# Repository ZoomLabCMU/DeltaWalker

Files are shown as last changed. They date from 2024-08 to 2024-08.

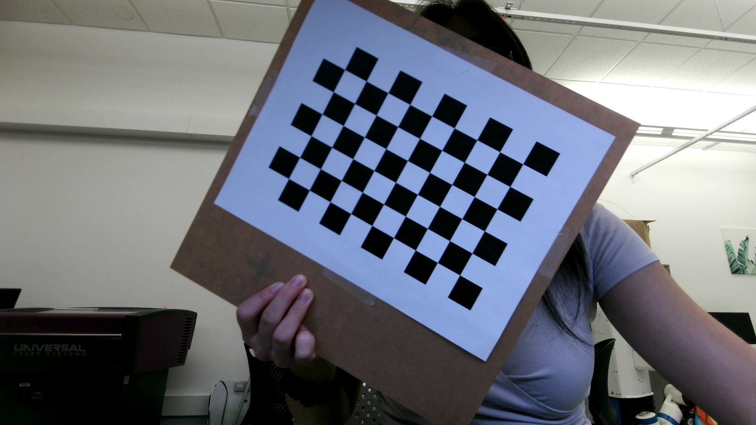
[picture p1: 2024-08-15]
testing/misc/camera_calibration/imgs/calib_30.png

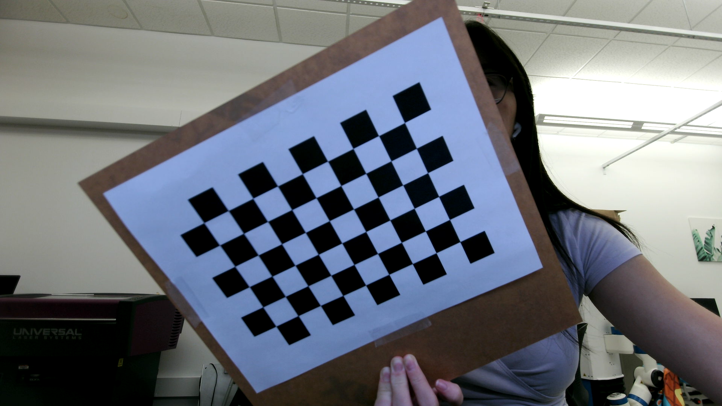
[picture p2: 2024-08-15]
testing/misc/camera_calibration/imgs/calib_4.png

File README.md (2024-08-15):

# DeltaWalker
Jennifer Yang, Zeynep Temel



**About This Project**

For more information about the project, please read Jennifer Yang's Masters Thesis:

https://www.ri.cmu.edu/publications/deltawalker-a-soft-linearly-actuated-delta-quadruped-robot/

This work was funded by the NSF under project Grant No.CMMI-2024794.

**Abstract**

Quadruped robots offer a versatile solution for navigating complex terrain, making them valuable for applications such as industrial automation or search and rescue. Although quadrupeds are more complex than bipeds, they are easier to balance and control and require fewer joints to actuate compared to hexapods. Traditional quadruped designs, however, often feature complex leg mechanisms that are difficult to scale and require many actuators.

We introduce the DeltaWalker, a novel quadruped robot that uses linearly actuated Delta robots as legs. Delta robots offer advantages such as precision and scalability, while still being able to move with three degrees of freedom. This design is inspired by DeltaHands, a 4-fingered hand robot with soft, 3D-printed linear Delta robots. We turn the DeltaHands upside down and adapt the design for locomotion. We explore various gait patterns, including manually designed and trajectory-optimized gaits, evaluated in both simulated and real-world environments. We also describe the system kinematics and investigate other capabilities, such as rotating in place. The findings from these evaluations demonstrate the potential of the DeltaWalker as a simpler, scalable, omnidirectional quadruped robot.

**About This Repo**

This repo contains code for the DeltaWalker Project, both the simulation code and the real-world testing code. 

**BibTeX**
```
@mastersthesis{Yang-2024-142602,
  author = {Jennifer Yang},
  title = {DeltaWalker: A Soft, Linearly Actuated Delta Quadruped Robot},
  year = {2024},
  month = {August},
  school = {Carnegie Mellon University},
  address = {Pittsburgh, PA},
  number = {CMU-RI-TR-24-23},
  keywords = {Delta Robot, Legged Robot, Quadruped Robot, Locomotion, Trajectory Optimization, Gaits},
}
```

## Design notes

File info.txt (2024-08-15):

Assorted files used by multiple folders

helpers - various helper functions
kinematics_delta - single delta kinematics
kineamtics_walker - walker kinematics
ocrl_paths - trajectory conversion class for trajectory optimized trajectories
path_gen - path generation class for manually designed trajectories
trajectories - manually designed trajectories

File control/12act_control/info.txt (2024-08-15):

12 actuator control code for computer to walker via cable
keyboard_operation - teleoperation
manual_traj_operation - commanding manually designed trajectories
ocrl_traj_operation - commanding trajectory-optimized trajectories
control_helpers - assorted helper functions for commanding trajectories
DeltaWalker - serial communication between computer and robot

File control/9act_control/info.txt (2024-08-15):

9 actuator control code for computer to walker via wifi
based on https://github.com/iamlab-cmu/DeltaHands

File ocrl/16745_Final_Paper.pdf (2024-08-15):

# Trajectory Generation for a Linearly Actuated Delta Quadruped Robot

Jennifer Yang
Robotics Institute
Carnegie Mellon University Pittsburgh, PA
jennifey@andrew.cmu.edu

Alfred Chang
Department of Mechanical Engineering Carnegie Mellon University Pittsburgh, PA
alfredc@andrew.cmu.edu

Jon Yeo
Department of Mechanical Engineering Carnegie Mellon University Pittsburgh, PA
jongwony@andrew.cmu.edu

Abstract—This paper introduces Delta Walker, a soft quadruped robot employing four 3D-printed prismatic delta robots. Initially designed as a hand-like manipulator, the Delta Walker operates within a diamond-shaped arrangement about its origin and exhibits compliant behavior due to the presence of soft links. The primary focus of this work lies in utilizing nonlinear trajectory optimization to generate walking trajectories for Delta Walker, which are subsequently verified through simulation using the inverse kinematics of the delta robots. The outcomes of this research contribute to advancements in control strategies for walking quadruped robots, particularly in trajectory optimization and simulation verification using inverse kinematics. Index Terms—prismatic delta robot, DIRCOL, trajectory optimization

I. INTRODUCTION

Delta Walker, Fig. 1, is a quadruped robot that uses 4 soft, 3D printed prismatic delta robots arranged in a diamond shape about the origin of the robot. It is approximately 15 cm × 15 cm wide and ranges from approximately 15 cm to 17 cm tall, depending on the motor actuation amounts. The robot initially operates as a hand-like manipulator, where the delta robots are configured as fingers to simulate dexterous hands with parallel fingertips. The parallelism and translational motions of these delta robots facilitate fingertip control, and the presence of soft links adds a degree of compliance [1]. In this paper, we present a method for trajectory optimization for the Delta Walker. We generate multiple trajectories that can be repeated for many iterations on robot to create full walking gaits. We ran these trajectories in simulation to verify that they would not cause the robot to fall over.

II. RELATED WORKS

The field of walking quadruped robots has seen significant advancements in control strategies aimed at achieving agile and robust locomotion. Various approaches have been explored to address the complexities of controlling multi-legged systems in diverse environments.
One notable focus in recent research has been on reinforcement learning (RL) algorithms for controlling quadruped robots. RL offers the advantage of learning controllers without explicit modeling of system dynamics, making it suitable

This work was funded by the NSF under project Grant No.CMMI-2024794.

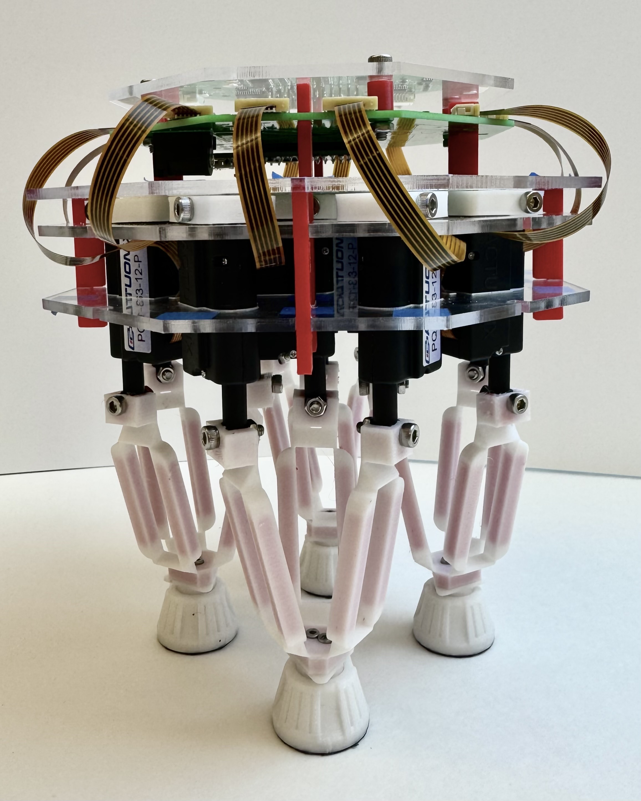
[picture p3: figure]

Fig. 1: Delta Walker

for handling noisy observations and controls. Platforms like RealAnt have been developed specifically for real-world reinforcement learning research, enabling the validation and evaluation of state-of-the-art RL algorithms on physical platforms [2].
Optimization-based control strategies have also played a crucial role in achieving robust locomotion for quadruped robots. These strategies include predictive controllers that reason about consequences iteratively and reactive controllers that focus on immediate actions. Model-based approaches offer advantages in safety considerations and generalization but face challenges in integrating perceptual streams [3]. Efforts have also been made to enhance the mechanical and electrical components of quadruped robots. Designs such as HAMR-F leverage advances in manufacturing, sensing, and energy storage to improve mechanical robustness, variable gait control, and payload capacity. These advancements contribute to achieving faster locomotion, improved heading control, and dynamic gaits with aerial phases [4].
Additionally, the development of low-cost and scalable quadruped robot platforms has opened avenues for research and education in control algorithms. Platforms like MIT minicheetah, Solo, and Stanford Doggo offer affordable options for exploring motion planning controllers and reinforcement learning in real-world settings [5]–[7].
The integration of advanced control algorithms with innovative hardware designs has paved the way for tackling challenges such as terrain adaptability, speed limitations, and payload capacity in walking quadruped robots. Ongoing research continues to focus on improving sample efficiency, safe exploration, and real-time adaptation of control strategies for agile and versatile locomotion in various environments. Overall, the interdisciplinary efforts in controls for walking quadruped robots encompass a wide range of techniques, from reinforcement learning and optimization-based strategies to mechanical enhancements and low-cost platform development, driving advancements in robotic locomotion and autonomy.

III. TRAJECTORY OPTIMIZATION

A. IPOPT

We chose the Interior Point OPTimizer solver – also termed IPOPT – as our solver of choice. This solver is meant for large scale non-linear optimization problems of continuous systems. We chose this solver because it fit with our problem setup of a quadratic cost function with a quadratic constraint. It is worth noting that all but the body torque constraint were linear constraints. The body torque constraint as specified in the Constraints section later is a function of both relative feet positions and the ground contact forces. Future work could target methods for reframing this constraint as a linear constraint to speed up computation.

B. Dynamics

Our system is represented by five point masses: one for the body and one for each foot. The state comprises the positions and velocities in the x, y, and z axes of these masses, resulting in a total of 12 degrees of freedom and 30 states. The system is governed by four control inputs, corresponding to forces along each leg. The ordering of the state and control vectors is as follows:

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
where p

(i)
is the position of the body or foot i in each axis, v

(i)
is the velocity of the body or foot i in each axis, and F

(i)
is the force along leg i.

We formulated our system dynamics as a linear equation governing forces:

mbI
mf I
mf I
mf I
mf I

v˙b
vf˙1
vf˙2
vf˙3
vf˙4

=

−m¨bg
−m¨f1
g
−m¨f2
g
−m¨f3
g
−m¨f4
g

+

−I −I −I −I
I | 0 | 0 | 0
0 | I | 0 | 0
0 | 0 | I | 0
0 | 0 | 0 | I

F1
F2
F3
F4

+

0 0 0 0
I 0 0 0
0 I 0 0
0 0 I 0
0 0 0 I

λ1
λ2
λ3
λ4

(2)

where mb is the mass of the body, mf is the mass of each foot, and λi

is the contact force on foot i.

C. Cost Function
We experimented with two different cost functions to evaluate their performance and found that Eqn. 4 yielded significantly better results.

J(x1:N , u1:N−1) =

N

X⁻¹

i=1

1
2

||xi − xg||²
2 +

1
2

||ui

||²
2
+

1
2

||xN − xg||²
2

(3)

The first cost function comprises a cost term for the distance between the current state and the goal state, along with a cost term for the internal body-to-foot forces. The state error cost term encourages the solver to reach the goal state quickly, as earlier attainment results in reduced net state error. The internal force cost term promotes lower overall control costs to minimize control effort and the forces sustained by the actuators. However, this cost function required the solver to take 2.5 times longer to generate a trajectory with minimal error compared to the subsequent cost function.

J(x1:N ) = X

N

i=1

1
2

||xi − xg||²
2

(4)

This cost function penalizes solely the error between the current state and the goal state, driving the solver to find a swift solution to reach the goal state without considering penalties for the control forces within the body. Utilizing this cost function, the solver produced the same trajectory, within minor tolerance, 2.5 times faster than Eqn. 3. Consequently, we employed this cost function for our optimization problem.

D. Optimization Problem & Constraints
In our problem setup, we employ a predefined set of knot points where one foot is permitted to be lifted off the ground while the other feet remain fixed to the ground. These knot points are stored in vectors named M0, M1, M2, M3, and M4, where the number designates which foot is permitted to be lifted off the ground, with M0 indicating that all four feet must maintain contact with the ground. The inclusion of M0 allows the robot sufficient time to shift its weight into the support polygon in preparation for the subsequent step.
The constraints applied to the optimization problem are as follows:

min

x1:N

J(x1:N )

1) Initial and goal state constraint:
| st x1 = xic | (1)
| xN = xg | (2)

Initial and goal constraints are used to dictate the starting and end states that the solver will optimize the trajectory for.
2) Dynamics constraint:

xk+1 = dynamics(xk, uk, λk) for k ∈ [1, N − 1] (3)

To guarantee adherence to the modeled dynamics during simulation, we impose an equality constraint on each subsequent state, derived from the dynamics solution of the preceding state.
3) Body height constraint:

0.053 ≤p

(b)
z ≤ 0.0605 for body z-height, k ∈ [1, N] (4)

To prevent the body from falling to the ground or flying into the sky, we apply a primal constraint on the z-height of the body position. The maximum z-height prevents scenarios where the robot flies into the sky and all feet lift off the ground. Conversely, the minimum z-height prevents the body from sinking too close to the ground, hindering the legs’ ability to lift. We set the maximum range of motion from 4.8cm to 6.8cm in height, and constrain the z-height of the robot body between 5.3cm and 6.05cm. This buffer ensures that the robot remains in a state where the legs can be lifted off the ground.
4) Foot height constraint:

p

(i)
z | ≥ 0 for i=1,2,3,4, k ∈ [1, N] | (5)

To prevent the foot from falling into the ground, we place a primal constraint on the z-height of the foot position.
5) Foot speed inequality constraint:

||v

(i)
||2 ≤ 0.015 for i=1,2,3,4, k ∈ [1, N] | (6)

Based on the physical specifications of the delta’s linear actuators, we impose a maximum speed of 15 mm/s on each foot.
6) Grounded foot velocity constraint:

||v

(i)
||2 = 0 for grounded foot, k ∈ [1, N] (7)

To prevent the solver from modeling frictionless contact, we apply a primal bound zero-velocity constraint on the feet that are determined to be fixed to the ground. It is reasonable to implement a zero-velocity constraint because the contact forces realizable by the motors are small compared to the body mass. This assumption also simplifies computation by eliminating the need to model a friction cone constraint.

7) Grounded foot z-height constraint:

p

(i)
z | ≤ 0.00025 for the grounded feet, k ∈ [1, N] | (8)

To further ensure that the robot never enters a dynamically unstable mode by lifting more than one foot, we enforce primal bound z-height constraint on the three feet that are meant to be grounded as dictated by the M’s. Without this constraint, we noticed that the solver would create a trajectory where multiple feet are lifted.
8) Ground contact force constraint:

λ

(i)
z | ≥ 0 for i=1,2,3,4, k ∈ [1, N − 1] | (9)

Since ground forces can only apply a normal force to an object in contact and cannot apply any force when an object is not in contact, we apply a constraint where the ground forces are non-negative if a foot is in contact with the ground, and a constraint where the ground force is zero if a foot is in the air.
9) Floating foot contact force constraint:

λ

(i)
z | = 0 for lifted feet k ∈ [1, N − 1] | (10)

Since the ground cannot exert a normal force on a foot that it is not in contact with, we place a primal bound on the lifted feet to ensure that the force is zero.
10) Body torque equality constraint:
X

4

i=1

λ

(i) × (p
(i) − p

(b)
) = 0 for k ∈ [1, N − 1] (11)

To prevent the body from reaching a state where it could tip over, we apply a net-zero torque constraint around the body center of mass (COM). This ensures that the body remains within the support polygon and never tips over. It’s worth noting that this constraint is the only quadratic constraint in our optimization problem. All other constraints in our optimization problem are linear constraints.
11) Foot position inequality constraints:

∥p

(ai)
x,y − p

(i)
x,y∥2 ≤ 0.0135 | (12)

p

(i)
z ≥ −0.0025 + (p

(ai)
z | − 0.058) | (13)

p

(i)
z ≤ 0.0075 + (p

(ai)
z | − 0.058) | (14)

for foot i, for k ∈ [1, N]

The Foot Position Inequality Constraints take the shape of a cylinder, with the circle in the x, y-plane, that moves in
the global frame fixed relative to p | (ai)
for each foot i. The
(p

(ai)
z − 0.058) serves as a z-offset for the lower and upper z bounds of the cylinder to translate with, as p
| (ai) | is initially
0.058 meters above the ground. The cylindrical bounds are determined based on the workspace of the delta actuator’s end effector, visualized as the space between two upward-facing convex paraboloids.
This cylindrical constraint restricts vertical motion of the body along the z axis in tandem with the other constraints.

As the cylinder moves in tandem with p

(ai)
(and consequently
with p

b
), exceeding a 0.0025-meter lift would elevate the cylinder above ground level, potentially conflicting with the Grounded Foot Z-Height Constraint. Conversely, lowering the body by more than 0.0075 meters would submerge the cylinder entirely below ground, rendering no feasible p

(i)
according to
the Foot Height Constraint.

IV. SIMULATION
The trajectory positions generated by the solver are in the world frame, where the ground plane is set to be z = 0. However, to calculate the motor actuation amounts to control the Delta Walker, these positions were shifted to the robot frame. For this, the z = 0 plane was shifted up to be coincident with the base plane of the robot, and the feet were placed on the negative z-axis. This adjustment was made to simplify the kinematic calculations. The motor actuation amounts for each delta were calculated using inverse kinematics for delta robots, considering the desired position of the COM and feet at each timestep. These actuation amounts were then input into the simulation environment.

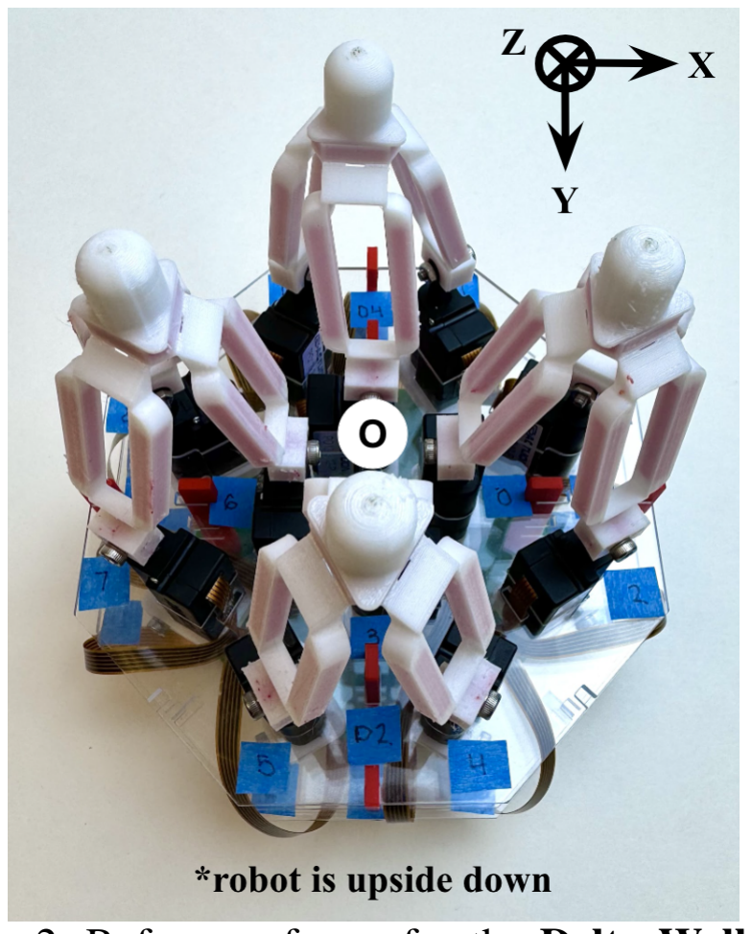
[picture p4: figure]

Fig. 2: Reference frame for the Delta Walker

The simulation of the Delta Walker was developed in Pybullet [8] using a simplified URDF model of the robot, as shown in Fig. 3, and set in the world frame. The objective of the simulation was to verify that the generated trajectories were quasi-statically stable and that the robot could reach the goal point. To simulate the motor actuation commands, we utilized Pybullet’s built-in P controller. We inputted the desired motor actuation amounts and imposed limits on the maximum force and velocity of the actuators to ensure realistic movement. Although the real robot employs a PID controller to command the motors, the built-in P controller sufficed for simulation purposes. Given that the trajectories should be quasi-statically stable and the robot moves slowly in the real world, we did not prioritize optimizing the simulated robot speed. We were able to track the world frame positions of the

COM and the feet of the robot in simulation and compared them to the desired positions of the robot from the generated trajectory.

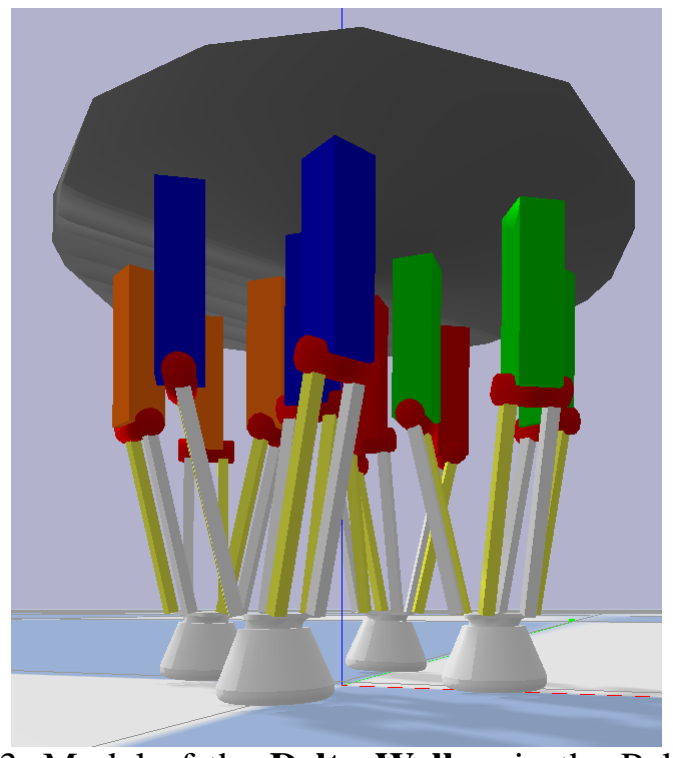
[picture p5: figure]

Fig. 3: Model of the Delta Walker in the Pybullet

V. RESULTS AND DISCUSSION
We generated three different trajectories with varying goal states and knot points. In the simulation, we tracked the positions of each point mass and calculated the mean square error of their positions. These variations and their resulting errors are listed in Table I. The feet were stepped in the order of Foot 3, Foot 2, Foot 4, and Foot 1.

TABLE I: Trajectory Generation Results

Trajectory Info | Mean Square Error (mm)
Label | Goal | Knot Points | Eb | E1 | E2 | E3 | E4
A | (20, 20, 53) | 40 | 8.0 | 7.7 | 7.7 | 7.0 | 7.0
B | (10, 10, 53) | 40 | 1.8 | 1.6 | 1.9 | 1.8 | 1.6
C | (20, 20, 53) | 80 | 3.0 | 3.8 | 4.6 | 3.0 | 3.1

Goal the goal position (x, y, z) of the body COM in mm.

For trajectories A and B, we opted to use 40 knot points, corresponding to each foot taking one step. For trajectory C, we chose to use 80 knot points, corresponding to each foot taking two steps. In trajectories A and C, we set the desired COM position to be 0.02 m away from the origin in the x and y axes. In trajectory B, we set the desired COM position to be closer to the origin, at 0.01 m away in the x and y axes. Trajectories B and C would take steps of size 0.01 m to reach the final point, whereas trajectory A would take a step of size 0.02 m.
Trajectory A, as shown in Fig. 4, exhibits the largest error. This occurred because the desired end point was too distant from the starting point, causing the actuators to reach their limits and the robot to take the maximum possible step. Additionally, the support polygon decreased in size after the first two steps, leading to tilting by the time the third foot (Foot 4) stepped in the sequence. Although it was meant to be

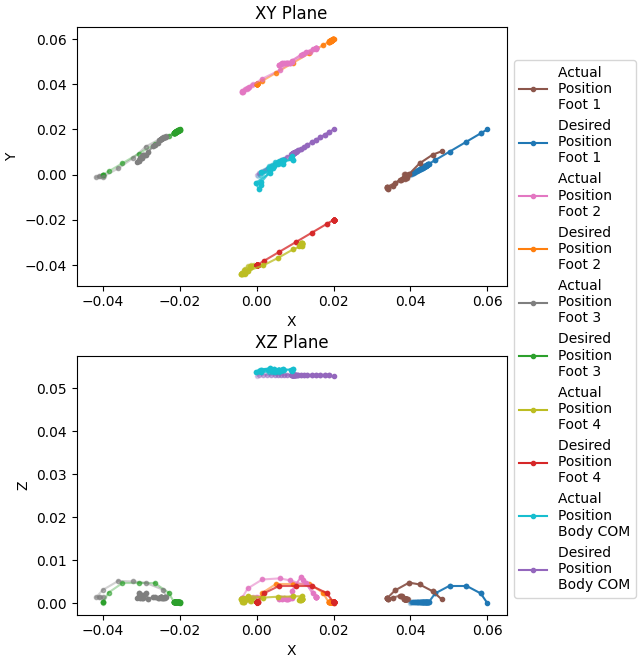
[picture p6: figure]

Fig. 4: Trajectory A Results

in the air, the robot leaned on that foot, resulting in instability and pushing rather than a stable step.

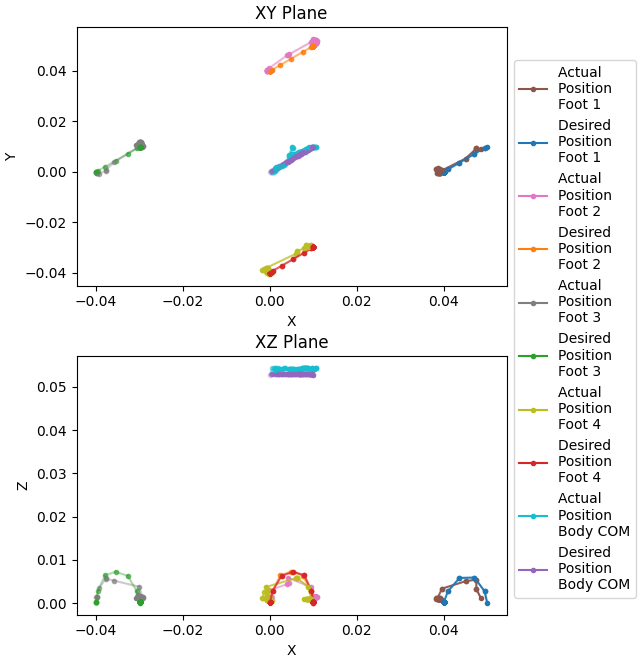
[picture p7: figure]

Fig. 5: Trajectory B Results

The error significantly improved with a smaller step size. Trajectory B, as depicted in Fig. 5, exhibits the smallest error among all trajectories. This improvement is attributed to the fact that the desired end point was within reach within the trajectory, ensuring that the actuator limits were not exceeded. Additionally, the support polygon remained wider, reducing the risk of the robot tipping over. Each foot lifted as expected, resulting in a stable step.

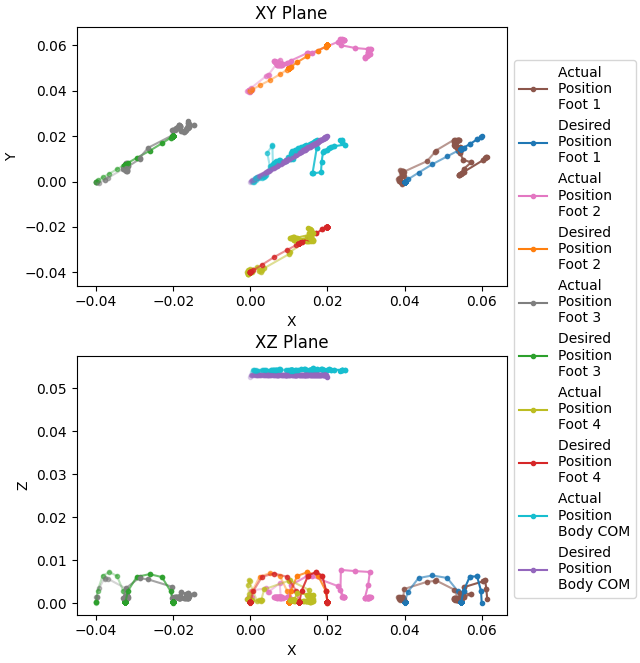
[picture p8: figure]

Fig. 6: Trajectory C Results

The error worsened when taking two steps despite the smaller step size. Trajectory C, illustrated in Fig. 6, exhibited better performance than Trajectory A but worse than Trajectory B. During the first set of steps, the second foot to lift (Foot
2) did not actually lift as the robot tilted towards it. Likewise, during the second set of steps, the third foot to lift (Foot 4) encountered the same issue. The steps were less stable because the generated trajectory had varying step sizes for each foot.

VI. CONCLUSIONS

We utilized trajectory optimization to generate three different trajectories for walking for the Delta Walker. We varied the goal states and knot points, allowing experimentation with the number of steps and step sizes. We found that using a smaller step size and generating only one set of steps was better for creating a quasi-statically stable gait. By repeating this gait multiple times, the robot has the potential to move far. Although taking larger steps or more sets of steps was not quasi-statically stable, they were still trajectories stable enough that the robot did not fall over, and the robot did progress forward towards the goal state. The gaits we generated and the parameters we experimented with will inform how to approach generating more gaits in the future.

VII. FUTURE WORK

One significant area of improvement is reducing solve time. Currently, the solver takes around 25 minutes to generate a trajectory with 40 knot points and 75 minutes to generate a trajectory with 80 knot points. Speed improvements can be found in a couple of areas. First, it may be possible to reformulate the Body Torque constraint, which is present to prevent the body from tipping over, into a linear constraint form. This would help simplify the complexity of the problem and allow us to use a linear optimization solver. Second, there may be other nonlinear optimizers that perform better for our problem size. The main reason we chose IPOPT over other solvers was that we were most familiar with it.
Additional work can be done to make the robot walk faster. We can explore relaxations on the body height constraint and foot position constraints to allow the robot to actuate closer to its limits. Additionally, for a more accurate model, we could model the contact patches more accurately using the geometric shape of the robot feet as opposed to just the current point mass model. Furthermore, we can explore different foot orderings to find a better walking gait or discover other types of gaits.
Beyond simulation, we can also apply this to the real robot and run tests to quantify the movement of the robot. We can run multiple iterations of the same trajectory and observe how far the robot moves not just in one set of steps but in multiple sets of steps, or combine different trajectories to create more complicated paths.

CODE AND VIDEOS

This research has not been published yet, so we cannot share the code at this time. However, videos of the trajectories in simulation, as well as some preliminary testing that has been done on the real robot, can be found here: https://tinyurl.com/ocrl-delta-walker. (https://drive.google.com/drive/folders/1QLCxWCHY97KjzdRRpfBpueAbO3D2707O?usp=sharing)

ACKNOWLEDGMENT

This research is associated with CMU’s Zoom Lab, led by Professor Zeynep Temel. The authors sincerely thank Professor Zeynep Temel, Professor Zachary Manchester, Arun Bishop, Zilin Si, and Sarvesh Patil for their assistance with this project.

REFERENCES

[1] Z. Si, K. Zhang, O. Kroemer and F. Z. Temel, ”DeltaHands: A Synergistic Dexterous Hand Framework Based on Delta Robots,” in IEEE Robotics and Automation Letters, vol. 9, no. 2, pp. 1795-1802, Feb. 2024, doi: 10.1109/LRA.2024.3349920.
[2] R. Boney, et al., ”RealAnt: An Open-Source Low-Cost Quadruped for Education and Research in Real-World Reinforcement Learning,” 2022. [Online]. Available: https://arxiv.org/abs/2011.03085.
[3] P. M. Wensing, M. Posa, Y. Hu, A. Escande, N. Mansard and A.
D. Prete, ”Optimization-Based Control for Dynamic Legged Robots,” in IEEE Transactions on Robotics, vol. 40, pp. 43-63, 2024, doi: 10.1109/TRO.2023.3324580.
[4] B. Goldberg et al., ”Power and Control Autonomy for High-Speed Locomotion With an Insect-Scale Legged Robot,” in IEEE Robotics and Automation Letters, vol. 3, no. 2, pp. 987-993, April 2018, doi: 10.1109/LRA.2018.2793355.
[5] B. Katz, J. D. Carlo and S. Kim, ”Mini Cheetah: A Platform for Pushing the Limits of Dynamic Quadruped Control,” 2019 International Conference on Robotics and Automation (ICRA), Montreal, QC, Canada, 2019, pp. 6295-6301, doi: 10.1109/ICRA.2019.8793865.
[6] Kim, D., Carlo, J.D., Katz, B., Bledt, G., & Kim, S. (2019). Highly Dynamic Quadruped Locomotion via Whole-Body Impulse Control and Model Predictive Control. ArXiv, abs/1909.06586.
[7] C. Gehring, S. Coros, M. Hutter, M. Bloesch, M. A. Hoepflinger and
R. Siegwart, ”Control of dynamic gaits for a quadrupedal robot,” 2013 IEEE International Conference on Robotics and Automation, Karlsruhe, Germany, 2013, pp. 3287-3292, doi: 10.1109/ICRA.2013.6631035.
[8] E. Coumans and Y. Bai, ”Pybullet, a python module for physics simulation for games, robotics and machine learning,” 2016.

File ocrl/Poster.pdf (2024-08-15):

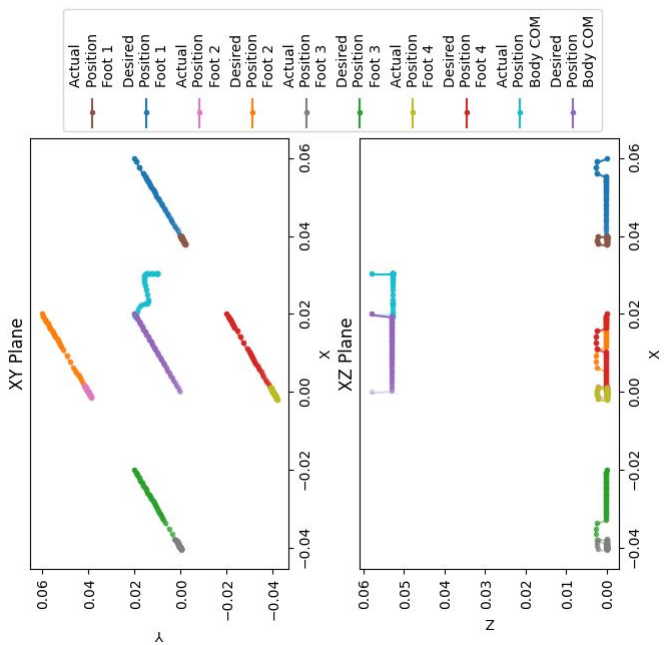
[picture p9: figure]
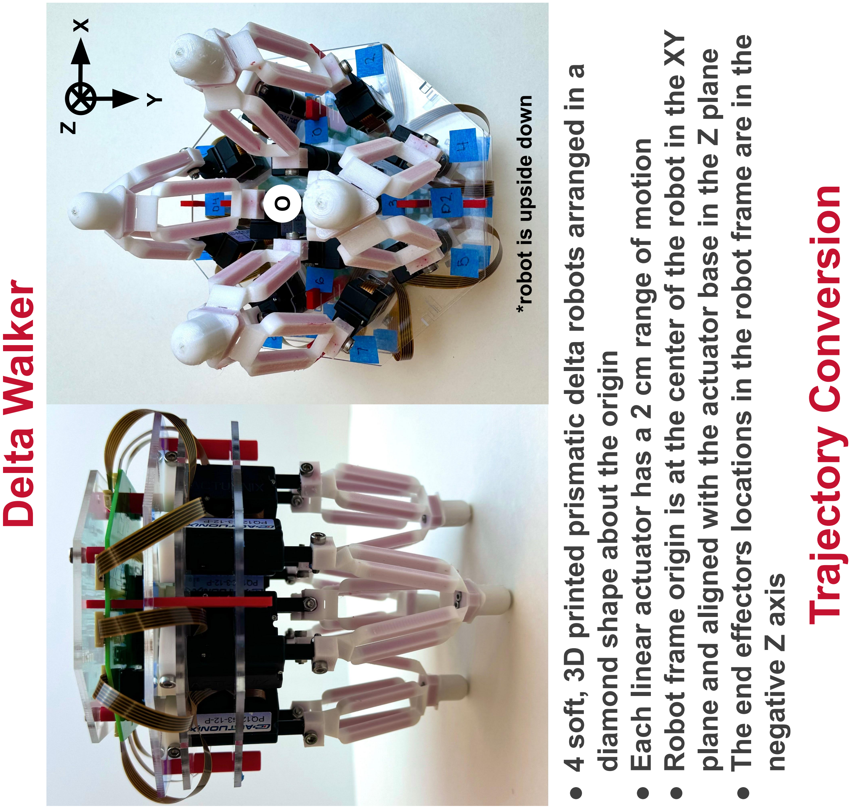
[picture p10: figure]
Delta Walker; diamond shape about the origin; negative Z axis; Trajectory Conversion; *robot is upside down

We use DIRCOL to generate our trajectory:

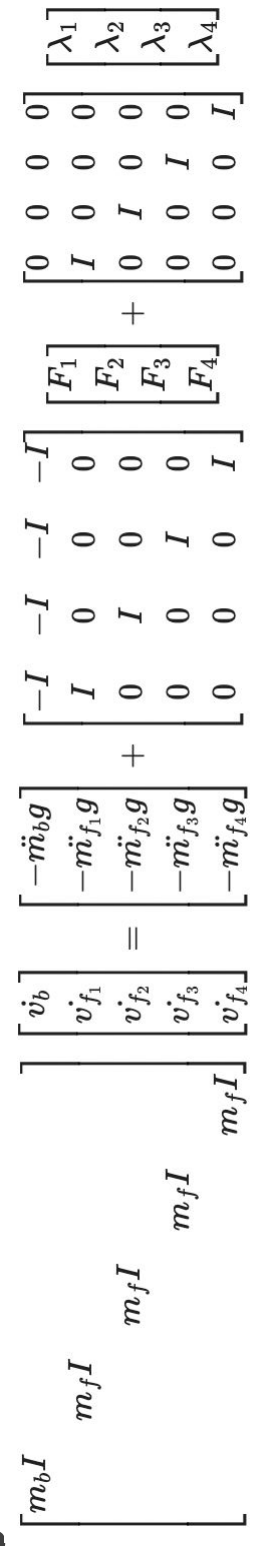
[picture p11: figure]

Dynamics

State

Control

Contact Forces

Costs

Constraints

### 1. Dynamics constraint

### 2. Body torque equality constraint

### 3. Foot velocity inequality constraint

### 4. Foot position inequality constraint

### 5. Body height constraint

### 6. Grounded foot velocity constraint

### 7. Grounded foot z-height constraint

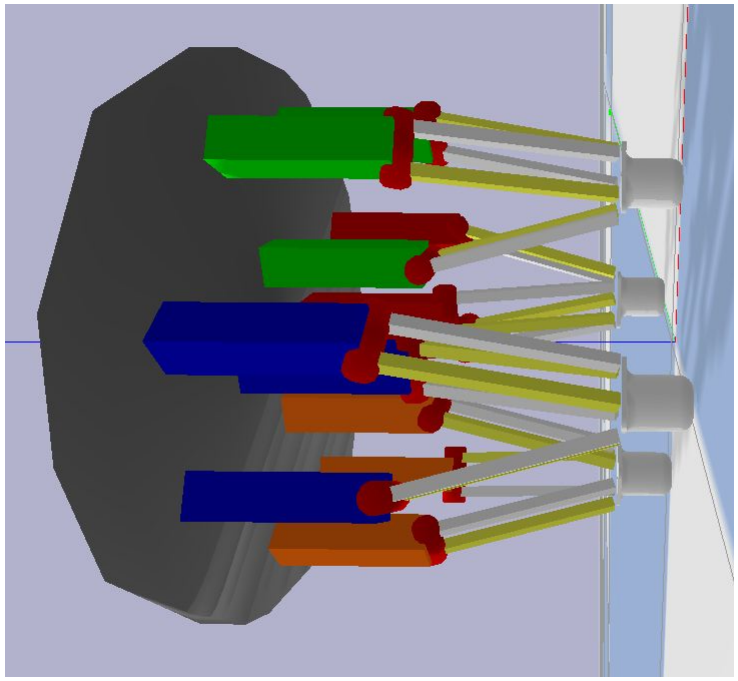
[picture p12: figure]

### 8. Floating foot ground force constraint

### 9. Grounded foot ground force constraint

## Paper ID:

2902

- Simulate the robot movement though Pybullet with a URDF model

of the robot

- Command motor actuation amounts using Pybullet’s built in P Control

function

- Use velocity and force bounds on the simulator to ensure realistic

speeds are being used

# Trajectory Generation for a Linearly Actuated Delta Quadruped Robot

## Jennifer Yang

1

## Alfred Chang

2

## Jon Yeo

2

### 1 School of Computer Science - Robotics Institute, Carnegie Mellon University

### 2 Carnegie Institute of Technology - Mechanical Engineering, Carnegie Mellon University

## Acknowledgements

This research is associated with CMU’s

Zoom Lab, led by Professor Zeynep Temel.

We extend a special thanks to Arun Bishop

for his help throughout the project.

- Use nonlinear trajectory optimization to generate a

walking trajectory for a soft, quadruped,

delta-actuated walking robot

- Verify the walking trajectory by simulating it, utilizing

the inverse kinematics of the delta robot

## Overview

## System Setup

- 4 soft, 3D printed prismatic delta robots arranged in a
- Each linear actuator has a 2 cm range of motion
- Robot frame origin is at the center of the robot in the XY plane and aligned with the actuator base in the Z plane
- The end effectors locations in the robot frame are in the

## Conclusion

We were able to find a trajectory for the robot to follow.

However, the robot moves very little. Currently, the generated trajectory is optimal to the solver, but constraints need to be tuned to produce a trajectory

that is reasonable for the robot.

## Future Work

- Continue to refine our system such that we can

generate better walking trajectories

- Evaluate the walking trajectories on the system in

simulation and the real world

## Results

## Simulation Setup

Delta Inverse
Kinematics

Desired COM
and Feet

Positions in

World Frame

Motor

Actuation

Amounts for
Each Foot

## Limitations

There is a large Sim2Real gap preventing the real robot

behavior from matching with the simulated results. Also, there is some simulation error that does not

match with the forward kinematics results.

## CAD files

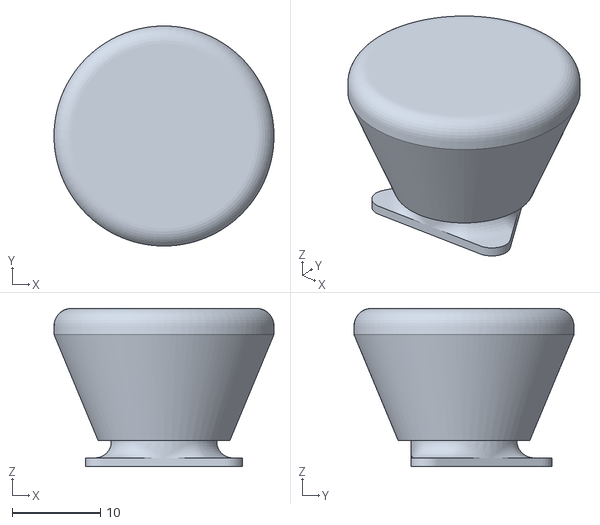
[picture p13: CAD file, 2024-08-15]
simulation/urdfs/feet/delta-feet-shoe-25mm-urdf.stl
25.0 x 25.0 x 18.0

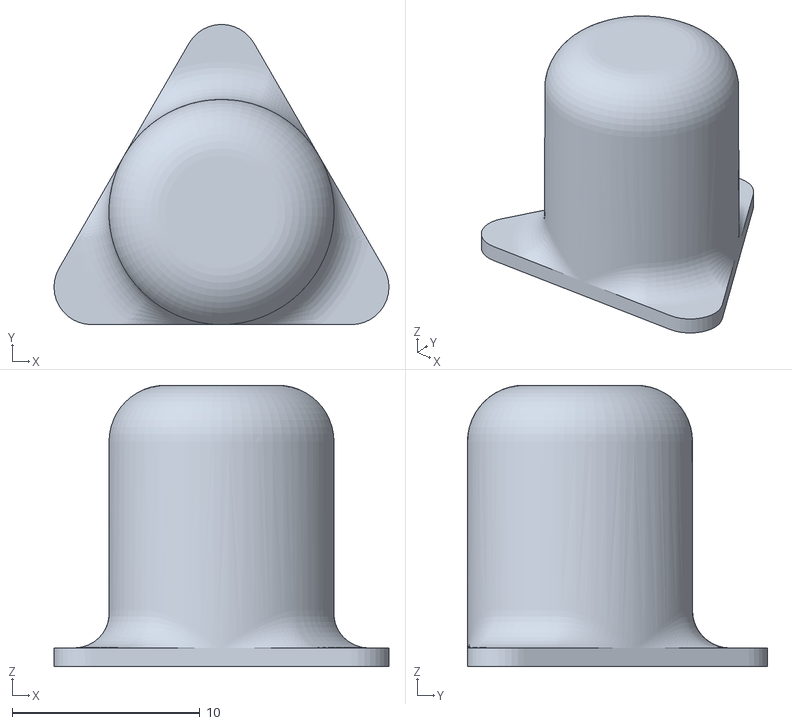
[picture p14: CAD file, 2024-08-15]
simulation/urdfs/feet/delta-feet-3mm-URDF.STL
17.9 x 16.0 x 15.0

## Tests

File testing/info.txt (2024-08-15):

Folders
    0_manual_design - manually designed trajectories results
    1_ocrl_trials - trajectory optimized trajectories results
    2_ocrl_variations - trajectory optimized trajectories with variance in foot ordering but same general pattern results
    3_ocrl_further_studies - further studies with trajectory optimized trajectories

Code
    1_video_adjust - convert raw video to mp4, undistort and crop the frames - saved in adjusted video folder
                        after video is saved as adjusted it is manually trimmed to remove excess time
                        when the robot is not doing anything and saved in trimmed video folder
    2_video_processing - foot detection on the trimmed video and annotated version of the video saved to annotated video folder
    3_video_speedup - speed up the videos - use videos from adjusted and saved to speedy folder
    4_data_processing - convert pixels to cm
    5_data_analysis - analyze the movement by comparing start to finish points with respect to the desired point
    6_step_process - user based interface to analyze the amount of time it takes for the robot to reach each step point to analyze single steps
    7_plotting_0/1/2/3 - plotting for the various folders of testing
    add_frame1 - speed up videos and annotate with estimation of the trajectories each foot follows
    livecam - livecam for viewing the testing setup with color detection
    processing_helpers - helper functions for data processing

Video folders
    You will need to make a folder in each of the main folders named "videos"
    That folder should have the following folders
        raw
        adjusted
        trimmed
        annotated
        speedy
        speedy_ann

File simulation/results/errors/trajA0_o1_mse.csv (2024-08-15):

# d1 | d2 | d3 | d4 | avg
2.70 | 3.04 | 2.61 | 2.90 | 2.78

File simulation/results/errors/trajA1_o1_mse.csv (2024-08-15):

# d1 | d2 | d3 | d4 | avg
3.76 | 3.42 | 2.74 | 3.42 | 3.31

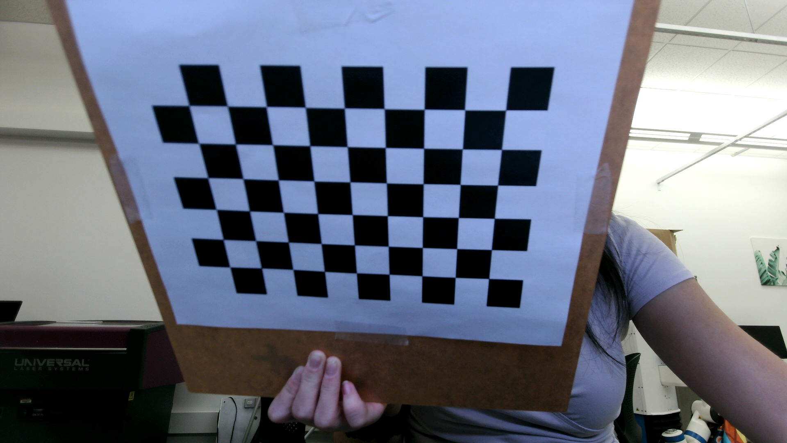
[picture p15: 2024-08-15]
testing/misc/camera_calibration/imgs/calib_36.png

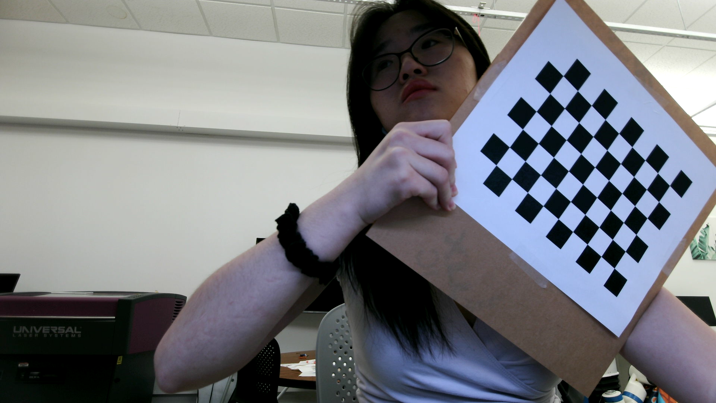
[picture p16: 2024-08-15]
testing/misc/camera_calibration/imgs/calib_27.png

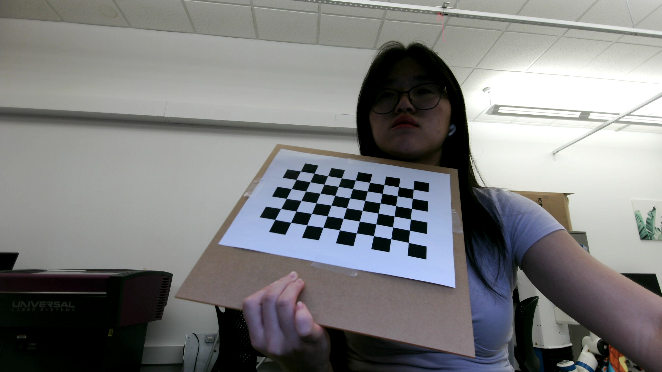
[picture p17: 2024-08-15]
testing/misc/camera_calibration/imgs/calib_37.png

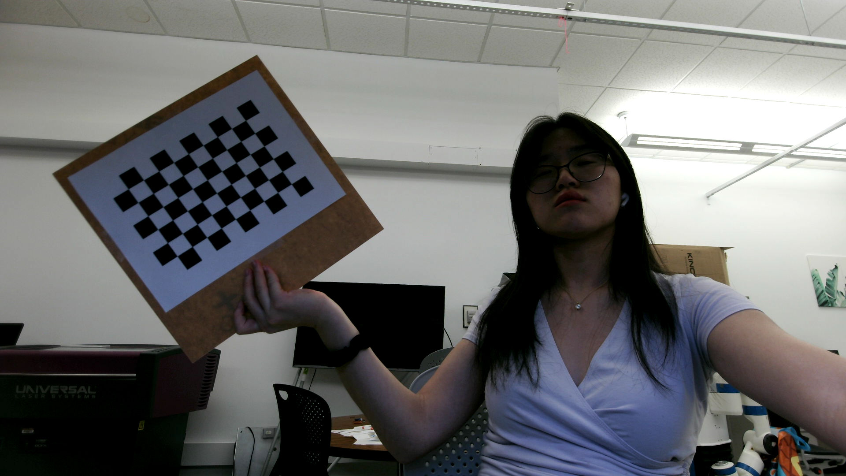
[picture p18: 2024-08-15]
testing/misc/camera_calibration/imgs/calib_39.png

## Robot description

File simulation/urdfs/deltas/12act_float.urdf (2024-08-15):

<?xml version="1.0"?>
<robot name="12act_float" >
 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
 <link name="world" />
 <joint type="fixed" name="base_joint" >
  <parent link="world" />
  <child link="base_link" />
  <origin xyz="0 0 0" rpy="0 0 0" />
 </joint>
 <link name="base_link" >
  <inertial >
   <mass value="0.25" />
   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
  </inertial>
  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
 </link>
 <joint type="prismatic" name="motor_joint_0" >
  <axis xyz="0 0 1" />
  <limit upper="0.02" velocity="1" lower="0" effort="100" />
  <parent link="base_link" />
  <child link="motor_link_0" />
  <origin xyz="0.02 0 0.01" rpy="0 0 1.5707963267948966" />
 </joint>
 <link name="motor_link_0" >
  <inertial >
   <mass value="0.021" />
   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
  </inertial>
  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
 </link>
 <joint type="prismatic" name="motor_joint_1" >
  <axis xyz="0 0 1" />
  <limit upper="0.02" velocity="1" lower="0" effort="100" />
  <parent link="base_link" />
  <child link="motor_link_1" />
  <origin xyz="0.05 0.017320508075688773 0.01" rpy="0 0 -0.5235987755982988" />
 </joint>
 <link name="motor_link_1" >
  <inertial >
   <mass value="0.021" />
   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
  </inertial>
  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
 </link>
 <joint type="prismatic" name="motor_joint_2" >
  <axis xyz="0 0 1" />
  <limit upper="0.02" velocity="1" lower="0" effort="100" />
  <parent link="base_link" />
  <child link="motor_link_2" />
  <origin xyz="0.05 -0.017320508075688773 0.01" rpy="0 0 -2.6179938779914944" />
 </joint>
 <link name="motor_link_2" >
  <inertial >
   <mass value="0.021" />
   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
  </inertial>
  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
 </link>
 <joint type="prismatic" name="motor_joint_3" >
  <axis xyz="0 0 1" />
  <limit upper="0.02" velocity="1" lower="0" effort="100" />
  <parent link="base_link" />
  <child link="motor_link_3" />
  <origin xyz="0 -0.02 0.01" rpy="0 0 0" />
 </joint>
 <link name="motor_link_3" >
  <inertial >
   <mass value="0.021" />
   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
  </inertial>
  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
 </link>
 <joint type="prismatic" name="motor_joint_4" >
  <axis xyz="0 0 1" />
  <limit upper="0.02" velocity="1" lower="0" effort="100" />
  <parent link="base_link" />
  <child link="motor_link_4" />
  <origin xyz="0.017320508075688773 -0.05 0.01" rpy="0 0 -2.0943951023931953" />
 </joint>
 <link name="motor_link_4" >
  <inertial >
   <mass value="0.021" />
   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
  </inertial>
  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
 </link>
 <joint type="prismatic" name="motor_joint_5" >
  <axis xyz="0 0 1" />
  <limit upper="0.02" velocity="1" lower="0" effort="100" />
  <parent link="base_link" />
  <child link="motor_link_5" />
  <origin xyz="-0.017320508075688773 -0.05 0.01" rpy="0 0 2.0943951023931953" />
 </joint>
 <link name="motor_link_5" >
  <inertial >
   <mass value="0.021" />
   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
  </inertial>
  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
 </link>
 <joint type="prismatic" name="motor_joint_6" >
  <axis xyz="0 0 1" />
  <limit upper="0.02" velocity="1" lower="0" effort="100" />
  <parent link="base_link" />
  <child link="motor_link_6" />
  <origin xyz="-0.02 0 0.01" rpy="0 0 -1.5707963267948966" />
 </joint>
 <link name="motor_link_6" >
  <inertial >
   <mass value="0.021" />
   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
  </inertial>
  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
 </link>
 <joint type="prismatic" name="motor_joint_7" >
  <axis xyz="0 0 1" />
  <limit upper="0.02" velocity="1" lower="0" effort="100" />
  <parent link="base_link" />
  <child link="motor_link_7" />
  <origin xyz="-0.05 -0.017320508075688773 0.01" rpy="0 0 2.6179938779914944" />
 </joint>
 <link name="motor_link_7" >
  <inertial >
   <mass value="0.021" />
   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
  </inertial>
  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
 </link>
 <joint type="prismatic" name="motor_joint_8" >
  <axis xyz="0 0 1" />
  <limit upper="0.02" velocity="1" lower="0" effort="100" />
  <parent link="base_link" />
  <child link="motor_link_8" />
  <origin xyz="-0.05 0.017320508075688773 0.01" rpy="0 0 0.5235987755982988" />
 </joint>
 <link name="motor_link_8" >
  <inertial >
   <mass value="0.021" />
   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
  </inertial>
  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
 </link>
 <joint type="prismatic" name="motor_joint_9" >
  <axis xyz="0 0 1" />
  <limit upper="0.02" velocity="1" lower="0" effort="100" />
  <parent link="base_link" />
  <child link="motor_link_9" />
  <origin xyz="0 0.02 0.01" rpy="0 0 3.141592653589793" />
 </joint>
 <link name="motor_link_9" >
  <inertial >
   <mass value="0.021" />
   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
  </inertial>
  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
 </link>
 <joint type="prismatic" name="motor_joint_10" >
  <axis xyz="0 0 1" />
  <limit upper="0.02" velocity="1" lower="0" effort="100" />
  <parent link="base_link" />
  <child link="motor_link_10" />
  <origin xyz="-0.017320508075688773 0.05 0.01" rpy="0 0 1.0471975511965976" />
 </joint>
 <link name="motor_link_10" >
  <inertial >
   <mass value="0.021" />
   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
  </inertial>
  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
 </link>
 <joint type="prismatic" name="motor_joint_11" >
  <axis xyz="0 0 1" />
  <limit upper="0.02" velocity="1" lower="0" effort="100" />
  <parent link="base_link" />
  <child link="motor_link_11" />
  <origin xyz="0.017320508075688773 0.05 0.01" rpy="0 0 -1.0471975511965976" />
 </joint>
 <link name="motor_link_11" >
  <inertial >
   <mass value="0.021" />
   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
  </inertial>
  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
 </link>
 <joint type="revolute" name="parallel_0_kneejoint" >
  <axis xyz="1 0 0" />
  <limit upper="3.141592653589793" velocity="1" lower="-3.141592653589793" effort="100" />
  <parent link="motor_link_0" />
  <child link="parallel_0_knee" />
  <origin xyz="0 0 0.04" rpy="0 0 0" />
 </joint>
 <link name="parallel_0_knee" >
  <inertial >
   <mass value="0.002" />
   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
  </inertial>
  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
 </link>
 <joint type="revolute" name="parallel_0_legjoint1" >
  <axis xyz="0 1 0" />
  <limit upper="1.5707963267948966" velocity="1" lower="-1.5707963267948966" effort="100" />
  <parent link="parallel_0_knee" />
  <child link="parallel_0_leg1" />
  <origin xyz="-0.005 0 0" rpy="0 0 0" />
 </joint>
 <joint type="revolute" name="parallel_0_legjoint2" >
  <axis xyz="0 1 0" />
  <limit upper="1.5707963267948966" velocity="1" lower="-1.5707963267948966" effort="100" />
  <parent link="parallel_0_knee" />
  <child link="parallel_0_leg2" />
  <origin xyz="0.005 0 0" rpy="0 0 0" />
 </joint>
 <link name="parallel_0_leg1" >
  <inertial >
   <mass value="0.005" />
   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
  </inertial>
  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
 </link>
 <link name="parallel_0_leg2" >
  <inertial >
   <mass value="0.005" />
   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
  </inertial>
  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
 </link>
 <joint type="revolute" name="parallel_1_kneejoint" >
  <axis xyz="1 0 0" />
  <limit upper="3.141592653589793" velocity="1" lower="-3.141592653589793" effort="100" />
  <parent link="motor_link_1" />
  <child link="parallel_1_knee" />
  <origin xyz="0 0 0.04" rpy="0 0 0" />
 </joint>
 <link name="parallel_1_knee" >
  <inertial >
   <mass value="0.002" />
   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
  </inertial>
  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
 </link>
 <joint type="revolute" name="parallel_1_legjoint1" >
  <axis xyz="0 1 0" />
  <limit upper="1.5707963267948966" velocity="1" lower="-1.5707963267948966" effort="100" />
  <parent link="parallel_1_knee" />
  <child link="parallel_1_leg1" />
  <origin xyz="-0.005 0 0" rpy="0 0 0" />
 </joint>
 <joint type="revolute" name="parallel_1_legjoint2" >
  <axis xyz="0 1 0" />
  <limit upper="1.5707963267948966" velocity="1" lower="-1.5707963267948966" effort="100" />
  <parent link="parallel_1_knee" />
  <child link="parallel_1_leg2" />
  <origin xyz="0.005 0 0" rpy="0 0 0" />
 </joint>
 <link name="parallel_1_leg1" >
  <inertial >
   <mass value="0.005" />
   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
  </inertial>
  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
 </link>
 <link name="parallel_1_leg2" >
  <inertial >
   <mass value="0.005" />
   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
  </inertial>
  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
 </link>
 <joint type="revolute" name="parallel_2_kneejoint" >
  <axis xyz="1 0 0" />
  <limit upper="3.141592653589793" velocity="1" lower="-3.141592653589793" effort="100" />
  <parent link="motor_link_2" />
  <child link="parallel_2_knee" />
  <origin xyz="0 0 0.04" rpy="0 0 0" />
 </joint>
 <link name="parallel_2_knee" >
  <inertial >
   <mass value="0.002" />
   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
  </inertial>
  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
 </link>
 <joint type="revolute" name="parallel_2_legjoint1" >
  <axis xyz="0 1 0" />
  <limit upper="1.5707963267948966" velocity="1" lower="-1.5707963267948966" effort="100" />
  <parent link="parallel_2_knee" />
  <child link="parallel_2_leg1" />
  <origin xyz="-0.005 0 0" rpy="0 0 0" />
 </joint>
 <joint type="revolute" name="parallel_2_legjoint2" >
  <axis xyz="0 1 0" />
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

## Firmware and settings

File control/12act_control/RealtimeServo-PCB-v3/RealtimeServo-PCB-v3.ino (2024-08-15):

#include <Wire.h>
#include <Adafruit_MotorShield.h>
#include <Adafruit_ADS1X15.h>
#include <math.h>

// https://github.com/nanopb/nanopb/tree/master

#define NUM_MOTORS 12
#define MY_ID 0

//######################################## Timer ###################
#define CPU_HZ 48000000
#define TIMER_PRESCALER_DIV 1024

// Create the three motor shield object I2C address input
Adafruit_MotorShield MC1 = Adafruit_MotorShield(0x60);
Adafruit_MotorShield MC2 = Adafruit_MotorShield(0x61);
Adafruit_MotorShield MC3 = Adafruit_MotorShield(0x62);

// Create 3 motor objects
// 1 - M3; 2 - M4; 3 - M1; 4 - M2
Adafruit_DCMotor *MC1_M1 = MC1.getMotor(3); // M1
Adafruit_DCMotor *MC1_M2 = MC1.getMotor(4); // M2
Adafruit_DCMotor *MC1_M3 = MC1.getMotor(1); // M3
Adafruit_DCMotor *MC1_M4 = MC1.getMotor(2); // M4

Adafruit_DCMotor *MC2_M1 = MC2.getMotor(3); // M1
Adafruit_DCMotor *MC2_M2 = MC2.getMotor(4); // M2
Adafruit_DCMotor *MC2_M3 = MC2.getMotor(1); // M3
Adafruit_DCMotor *MC2_M4 = MC2.getMotor(2); // M4

Adafruit_DCMotor *MC3_M1 = MC3.getMotor(3); // M1
Adafruit_DCMotor *MC3_M2 = MC3.getMotor(4); // M2
Adafruit_DCMotor *MC3_M3 = MC3.getMotor(1); // M3
Adafruit_DCMotor *MC3_M4 = MC3.getMotor(2); // M4

// create array of pointers to motor objects
Adafruit_DCMotor* motors[NUM_MOTORS] = {MC1_M1, MC1_M2, MC1_M3, MC1_M4,
                                        MC2_M1, MC2_M2, MC2_M3, MC2_M4,
                                        MC3_M1, MC3_M2, MC3_M3, MC3_M4
                                       };

// create object to access off-board analog-to-digital converter
Adafruit_ADS1015 ADC1; //ADC1 // ADC2
Adafruit_ADS1015 ADC2;
Adafruit_ADS1015 ADC3;

Adafruit_ADS1015* adcs[NUM_MOTORS] = {&ADC1, &ADC1, &ADC1, &ADC1,
                                      &ADC2, &ADC2, &ADC2, &ADC2,
                                      &ADC3, &ADC3, &ADC3, &ADC3,
                                     };
int channels[NUM_MOTORS] = {0, 1, 2, 3,
                            0, 1, 2, 3,
                            0, 1, 2, 3
                           };

//#################################### GLOBAL VARIABLES ##################################//

/* TBD if needed - Existed in the code but wasn't used by anything
  float max_motor_speed[NUM_MOTORS] =     {15.0, 15.0, 15.0, 15.0, 15.0, 15.0, 15.0, 15.0, 15.0, 15.0, 15.0, 15.0};
  float max_motor_position[NUM_MOTORS] =  {19.5, 19.5, 19.5, 19.5, 19.5, 19.5, 19.5, 19.5, 19.5, 19.5, 19.5, 19.5};
  float desired_motor_speed[1];
  int sampleTime = 0;
  float time_left = max(durations[current_trajectory_point] - last_time, 0.1);
  const int numChars = 3000;
*/

//--------------------------------------------------------------------------------------------------------------------------------------------------------------------------------------------------------

// Misc
float pi = 3.1415926535;

// Calculate based on max input size expected for one command
#define MAX_INPUT_SIZE 20000

// Sending and Receiving Information
char inputString[MAX_INPUT_SIZE + 1];
bool newData = false;
int currentStringLength = 0;
int ndx = 0;
bool recvInProgress = false;
char startMarker = '<';
char endMarker = '>';

// Stop Command Global
bool stop_flag = false;

// Conversions ******************************************************     CHECK THIS      ***********************************
#define ADC2M 0.012 //ADC reading to pos in [mm]
#define VEL2CMD 17.0 // vel [mm/s] to motor command val [x/+-255]

// Displaying Information
String joint_states;

//--------------------------------------------------------------------------------------------------------------------------------------------------------------------------------------------------------

// Position and Velocity Information
int motor_val[NUM_MOTORS] = {0, 0, 0, 0, 0, 0, 0, 0, 0, 0, 0, 0};  // pre-conversion to mm
float joint_positions[NUM_MOTORS] = {0.0, 0.0, 0.0, 0.0, 0.0, 0.0, 0.0, 0.0, 0.0, 0.0, 0.0, 0.0};       // mm
float joint_velocities[NUM_MOTORS] = {0.0, 0.0, 0.0, 0.0, 0.0, 0.0, 0.0, 0.0, 0.0, 0.0, 0.0, 0.0};      // mm/s
float last_joint_positions[NUM_MOTORS] = {0.0, 0.0, 0.0, 0.0, 0.0, 0.0, 0.0, 0.0, 0.0, 0.0, 0.0, 0.0};  // mm

// Error Information
float last_joint_errors[NUM_MOTORS] = {0.0, 0.0, 0.0, 0.0, 0.0, 0.0, 0.0, 0.0, 0.0, 0.0, 0.0, 0.0};     // mm
float joint_errors[NUM_MOTORS] = {0.0, 0.0, 0.0, 0.0, 0.0, 0.0, 0.0, 0.0, 0.0, 0.0, 0.0, 0.0};          // mm

float position_threshold = 1.0;   // mm  //***********************      CHANGE THIS?      ***********************************

// Trajectory Information
float desired_joint_positions[1][NUM_MOTORS]; // Typically num_trajectory_points x NUM_MOTORS
float durations[1];
int num_trajectory_points = 0;
int current_trajectory_point = 0;
bool position_trajectory = false;

float reset_pos = 0.5; // mm //**********************************      CHANGE THIS!      ***********************************

//--------------------------------------------------------------------------------------------------------------------------------------------------------------------------------------------------------

// Time Information
float last_time = 0.0;                // s
unsigned long current_arduino_time;   // ms
unsigned long last_arduino_time;      // ms
float time_elapsed;                   // s

//--------------------------------------------------------------------------------------------------------------------------------------------------------------------------------------------------------

// PID
float k_p = 3.0; // 2.5 // 3.0; // 0.2 // 5.0 // 2.0 
float k_i = 0.5;
float k_d = 0.02;

float _cmdPos_error[NUM_MOTORS];
float _cmdPos_integral_error[NUM_MOTORS];
float _cmdPos_derivative_error[NUM_MOTORS];

//--------------------------------------------------------------------------------------------------------------------------------------------------------------------------------------------------------
// INTEGRATING CHRIS CODE - CHANGES MAY NEED TO BE MADE HERE

// Max values
float tf_max = 0;       // s - maximum completion time needed to move an actuator

// Commands
float _joint_positionsCmd[NUM_MOTORS] =   {0.0, 0.0, 0.0, 0.0, 0.0, 0.0, 0.0, 0.0, 0.0, 0.0, 0.0, 0.0};
float _joint_velocitiesCmd[NUM_MOTORS] =  {0.0, 0.0, 0.0, 0.0, 0.0, 0.0, 0.0, 0.0, 0.0, 0.0, 0.0, 0.0};
float _refCmd[NUM_MOTORS] =               {0.0, 0.0, 0.0, 0.0, 0.0, 0.0, 0.0, 0.0, 0.0, 0.0, 0.0, 0.0};
float _motorCmd[NUM_MOTORS] =             {0.0, 0.0, 0.0, 0.0, 0.0, 0.0, 0.0, 0.0, 0.0, 0.0, 0.0, 0.0};

//--------------------------------------------------------------------------------------------------------------------------------------------------------------------------------------------------------

// Receive Data
void recvWithStartEndMarkers() {
  char rc;

//  Serial.println();
//  Serial.println("RECIEVING");
  
  while (Serial.available() > 0 && newData == false) {
    rc = Serial.read();

    if (recvInProgress == true) {
      if (rc != endMarker) {
        inputString[ndx] = rc;
        ndx++;
      }
      else {
        inputString[ndx] = '\0'; // terminate the string
        recvInProgress = false;
        currentStringLength = ndx;
        ndx = 0;
        newData = true;
      }
    }
    else if (rc == startMarker) {
      recvInProgress = true;
    }
  }
//  Serial.println(inputString);
//  Serial.println("DONE RECIEVING");
//  Serial.println();
}

//--------------------------------------------------------------------------------------------------------------------------------------------------------------------------------------------------------
// STOP COMMAND
// Immediately halts everything by setting all the motor control pins to LOW and sets the stop_flag to true.
// Remember to publish a false msg to restart the robot.

void stop(bool stop_msg) {
  // If the stop_msg contains true, stop all of the motors
  if (stop_msg)
  {
    // set stop_flag to true
    stop_flag = true;

    // Turn off all motors
    for (int i = 0; i < NUM_MOTORS; i++)
    {
      if (motors[i] != NULL) {
        motors[i]->run(RELEASE);
      }
    }
  }
  // Otherwise if the stop_msg contains false, set the stop_flag back to false
  else
  {
    stop_flag = false;
  }
}

//--------------------------------------------------------------------------------------------------------------------------------------------------------------------------------------------------------
// RESET COMMAND
// Resets the robot's desired positions to the default positions.

void resetJoints() {
  num_trajectory_points = 1;
  durations[0] = 4.0;
  for (int i = 0; i < NUM_MOTORS; i++)
  {
    desired_joint_positions[0][i] = reset_pos;
  }

  position_trajectory = true;
  current_trajectory_point = 0;
  last_time = 0.0;
}

//--------------------------------------------------------------------------------------------------------------------------------------------------------------------------------------------------------
// STATE UPDATES

// Position Update
void updateJointPositions()
{
  for (int i = 0; i < NUM_MOTORS; i++)
  {
    if (motors[i] != NULL)
    {
      motor_val[i] = adcs[i]->readADC_SingleEnded(channels[i]);
      joint_positions[i] = motor_val[i] * ADC2M; // 3.0 * 0.02 / 5.0; // 1 bit = 2mV @ 4.096 FSR 0.02 mm stroke 3.3V range // 100mm / 1650 analog reading
    }
  }
}

// Previous Position Update
void updatePreviousJointPositions()
{
  for (int i = 0; i < NUM_MOTORS; i++)
  {
    if (motors[i] != NULL)
    {
      last_joint_positions[i] = joint_positions[i];
    }
  }
}

// Time Update
void updateTime() {
  // Update time
  current_arduino_time = millis();
  time_elapsed = float(current_arduino_time - last_arduino_time) / 1000.0;
  last_time += time_elapsed;

  // Store time
  last_arduino_time = current_arduino_time;
}

// Velocity Update
void updateVelocity() {
  for (int i = 0; i < NUM_MOTORS; i++)
  {
    joint_velocities[i] = (joint_positions[i] - last_joint_positions[i]) / time_elapsed;
  }
}

// State Update
void updateState() {
  updatePreviousJointPositions();
  updateTime();
  updateJointPositions();
  updateVelocity(); 
}

//--------------------------------------------------------------------------------------------------------------------------------------------------------------------------------------------------------
// POSITION TRAJECTORY
// Stores the Position Trajectory to desired_joint_positions
void positionTrajectory()
{
  String received = "p ";

  Serial.println();
  Serial.print(received);

  char *strtokIndx; // this is used by strtok() as an index

  strtokIndx = strtok(inputString, ",");     // get the first part - the string
  strtokIndx = strtok(NULL, ","); // this continues where the previous call left off
  num_trajectory_points = atoi(strtokIndx);

  for (int i = 0; i < num_trajectory_points; i++)
  {
    received = "p ";
    strtokIndx = strtok(NULL, ",");         // this continues where the previous call left off
    durations[i] = atof(strtokIndx);
    Serial.print("durations i");
    Serial.println(durations[i]);
    received += String(durations[i]) + " ";

    for (int j = 0; j < NUM_MOTORS; j++)
    {
      strtokIndx = strtok(NULL, ",");       // this continues where the previous call left off
      desired_joint_positions[i][j] = atof(strtokIndx);
      received += String(desired_joint_positions[i][j], 4) + " ";
    }

    Serial.print("Trajectory Point ");
    Serial.print(i);
    Serial.print(": \t");
    Serial.println(received);
  }
  position_trajectory = true;
  current_trajectory_point = 0;
  last_time = 0.0;

  Serial.print("Number of trajectory points \t");
  Serial.println(num_trajectory_points);
}

//--------------------------------------------------------------------------------------------------------------------------------------------------------------------------------------------------------
// MOVE DELTA USING P CONTROL
// Each actuator moves at its own rate

void moveDeltaPosition()
{
  bool reached_point = true;
  Serial.println();
  
  Serial.print("E, ");
  // Check if any of the motors have not reached their desired position
  for (int idx = 0; idx < NUM_MOTORS; idx++)
  {
    if (motors[idx] != NULL)
    {
      updateJointPositions();
      joint_errors[idx] = joint_positions[idx] - desired_joint_positions[current_trajectory_point][idx];
      
      Serial.print(joint_errors[idx], 4);
      Serial.print(",");

      if (fabs(joint_errors[idx]) > position_threshold)
      {
        reached_point = false;
      } 
      // Stop motor if it's reached its desired point (within the threshold)
      else 
      {
        motors[idx]->setSpeed(0);
        motors[idx]->run(RELEASE);
      }
    }
  }

  Serial.println();
  
  // If all motors have reached their desired position, move onto the next trajectory
  if (reached_point)
  {
    Serial.println("reached point, onto next trajectory");
    current_trajectory_point += 1;
  }

  // P control if it has not reached the desired point yet
  if (current_trajectory_point < num_trajectory_points)
  {
    for (int i = 0; i < NUM_MOTORS; i++)
    {
      if (motors[i] != NULL)
      {
        // Move forwards
        if (joint_errors[i] > position_threshold)
        {
          //  Serial.println("Forwarding...");
          float pid = k_p * joint_errors[i];
          int motor_speed = (int)(min(max(0.0, pid), 1.0) * 255.0); //change it to use duration input
          // Serial.print(motor_speed);
          motors[i]->setSpeed(motor_speed);
          motors[i]->run(FORWARD);
        }
        // Move backwards
        else if (joint_errors[i] < -position_threshold)
        {
          //  Serial.println("Backwarding...");
          float pid = k_p * joint_errors[i];
          int motor_speed = (int)(min(max(-1.0, pid), 0.0) * -255.0);
          // Serial.print(motor_speed);
          motors[i]->setSpeed(motor_speed);
          motors[i]->run(BACKWARD);
        }
        // Do nothing
        else
        {
          //  Serial.println("Doing nothing...");
          motors[i]->setSpeed(0);
          motors[i]->run(RELEASE);
        }
      }
    }
  }
  // Do nothing if it has reached the desired point 
  else
  {
    for (int i = 0; i < NUM_MOTORS; i++)
    {
      if (motors[i] != NULL) {
        motors[i]->setSpeed(0);
        motors[i]->run(RELEASE);
      }
    }
    Serial.println("end of all available trajectories");
    position_trajectory = false; //finished moving all commands
  }
}

//--------------------------------------------------------------------------------------------------------------------------------------------------------------------------------------------------------
// MOTOR COMMANDS

void cmdPos(float qCmd[NUM_MOTORS])
{
  for (int i = 0; i < NUM_MOTORS; i++) {
    _joint_positionsCmd[i] = qCmd[i];
  }
}

void cmdVel(float q_dotCmd[NUM_MOTORS])
{
//  Serial.println();
//  Serial.println("cmdVel");
  for (int i = 0; i < NUM_MOTORS; i++) {
    _joint_velocitiesCmd[i] = q_dotCmd[i];
//    Serial.print("\t ");
//    Serial.print(q_dotCmd[i]);
    _refCmd[i] = q_dotCmd[i] * VEL2CMD;
  }
//  Serial.println();
}

void positional_PID(float PID_Cmd[NUM_MOTORS]) {
  for (int i=0; i<NUM_MOTORS; i++) {
    float error = _joint_positionsCmd[i] - joint_positions[i];
    _cmdPos_integral_error[i] = _cmdPos_integral_error[i] + error * (time_elapsed);
    _cmdPos_derivative_error[i] = (error - _cmdPos_error[i]) / (time_elapsed);
    _cmdPos_error[i] = error;
  
    PID_Cmd[i] = (k_p*_cmdPos_error[i] + 
                  k_i*_cmdPos_integral_error[i] + 
                  k_d*_cmdPos_derivative_error[i]);
  }
}

void send_motorCmd()
{
//  Serial.println();
//  Serial.println("SEND MOTOR COMMAND");
  
  for (int i = 0; i < NUM_MOTORS; i++) {
    int motor_cmd_val = _motorCmd[i];
    motor_cmd_val = min(max(motor_cmd_val, -255), 255); // Clip to safe bounds

//    Serial.print("\tMotor ");
//    Serial.print(i);
//    Serial.print(" \t\t_motorCmd ");
//    Serial.print(_motorCmd[i]);
//    Serial.print(" \t\t Clipped value ");
//    Serial.print(motor_cmd_val);
//    Serial.print(" \t\t speed ");
//    Serial.println((int)(abs(motor_cmd_val)));

    int motor_threshold = 0;
//    Serial.println(motor_cmd_val);
    motors[i]->setSpeed((int)(abs(motor_cmd_val)));
//    motors[i]->setSpeed(100);
    if (motor_cmd_val > motor_threshold) { // 20 threshold?
//      Serial.println("FORWARD");
      motors[i]->run(BACKWARD);
    } else if (motor_cmd_val < motor_threshold) {
//      Serial.println("BACKWARD");
      motors[i]->run(FORWARD);
    } else {
//      Serial.println("RELEASE");
      motors[i]->run(RELEASE);
    }
  }
}

void driveController()
{
  updateState();

//  Serial.println();
//  Serial.println("DRIVE CONTROLLER");

  float PID_Cmd[NUM_MOTORS];
  positional_PID(PID_Cmd);

  for (int i = 0; i < NUM_MOTORS; i++) {
    float error = _joint_positionsCmd[i] - joint_positions[i];
//    float error = desired_joint_positions[current_trajectory_point][i] - joint_positions[i];
//    float p_command = P;

//    Serial.print("\t Motor ");
//    Serial.print(i);
//    Serial.print(" \t\t pos cmd ");
//    Serial.print(_joint_positionsCmd[i]);
//    Serial.print(" \t\t cur pos ");
//    Serial.print(joint_positions[i]);
//    Serial.print(" \t\t err ");
//    Serial.print(error);
//    Serial.print(" \t\t des pos ");
//    Serial.print(desired_joint_positions[current_trajectory_point][i]);
//    Serial.print("\t\t ref_cmd ");
//    Serial.print(_refCmd[i]);
//    Serial.print(" \t\t pid_command ");
//    Serial.println(PID_Cmd[i]);
    
    _motorCmd[i] = (int)(_refCmd[i] + PID_Cmd[i] * VEL2CMD); //TODO change 0.5?
  }
  send_motorCmd();
}

//--------------------------------------------------------------------------------------------------------------------------------------------------------------------------------------------------------
// TRAJECTORIES 

// Get maximum tf
void ramp_tf(float tf[NUM_MOTORS], float vmax, float amax)
{
  float tr;
  float tm;

  float delta_x;

  tf_max = 0;
  for (int idx = 0; idx < NUM_MOTORS; idx++)
  {
    delta_x = abs(desired_joint_positions[current_trajectory_point][idx] - joint_positions[idx]);
    
    tr = min(delta_x / vmax, vmax / amax);      
    tm = max(0, delta_x / vmax - vmax / amax);
    tf[idx] = 2 * tr + tm;

//    Serial.println();
//    Serial.print("Ramp tf calculation for motor ");
//    Serial.println(idx);
//    Serial.print("tf: ");
//    Serial.print(tf[idx]);
//    Serial.print(" \t tf_max prev: ");
//    Serial.print(tf_max);
//    Serial.print(" \t dx/vmax: ");
//    Serial.print(delta_x / vmax);
//    Serial.print(" \t vmax/amax: ");
//    Serial.print(vmax / amax);
//    Serial.print(" \t 0 \t dx/vmax - vmax/amax: ");
//    Serial.print(delta_x / vmax - vmax / amax);
//    Serial.print(" \t tf_max new: ");
    tf_max = max(tf_max, tf[idx]);
//    Serial.println(tf_max);
  }
}

// Modify qCmd with the x(t) values of a ramp traj
void ramp_pos(float t, float qCmd[NUM_MOTORS], float v[NUM_MOTORS], float amax_ref)
{ 
  float vmax;
  float amax;

//  Serial.println();
  
  for (int i = 0; i < NUM_MOTORS; i++)
  {
    float delta_x = desired_joint_positions[current_trajectory_point][i] - joint_positions[i];
    
    if (delta_x < 0) {
      vmax = -v[i];
      amax = -amax_ref;
    } else {
      vmax = v[i];
      amax = amax_ref;
    }
    
    float tr = min(delta_x / vmax, vmax / amax);
    float tm = max(0, delta_x / vmax - vmax / amax);
  
//    Serial.print(i);
//    Serial.print("\t");
//    Serial.print(t);
//    Serial.print("\t");
//    Serial.print(tr);
//    Serial.print("\t");
//    Serial.print(tm);
//    Serial.print("\t");
//    Serial.print(joint_positions[i]);
//    Serial.print("\t");
    
    // Piece wise integration
    if (t < tr) {
//      Serial.println("C1");
      qCmd[i] = joint_positions[i] + 0.5 * amax * pow(t, 2);
    } else if (tr <= t & t < tr + tm) {
//      Serial.println("C2");
      qCmd[i] = joint_positions[i] + (0.5 * amax * pow(tr, 2)) + vmax * (t - tr);
    } else if (tr + tm <= t & t < 2 * tr + tm) {
//      Serial.println("C3");
      qCmd[i] = joint_positions[i] + (0.5 * amax * pow(tr, 2)) + (vmax * tm) + (vmax * (t - tm - tr) - 0.5 * amax * pow(t - tm - tr, 2));
    } else {
//      Serial.println("C4");
      qCmd[i] = desired_joint_positions[current_trajectory_point][i];
    }
  }
}
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
void loop()
{
  // Mode selection
  recvWithStartEndMarkers();
  Serial.print("new data tf ");
  Serial.println(newData);
  if (newData) {
    Serial.println(inputString);
    switch (inputString[0]) {
      // Stop Command
      case 's':
        stop(inputString[2] - '0');
        break;
      // Reset Command
      case 'r':
        resetJoints();
        break;
      // Position Command
      case 'p':
        positionTrajectory();
        break;
      default:
        // do nothing
        break;
    }
    newData = false;
  }

  // If the robot is not currently in the stop mode, move
  if (!stop_flag)
  {
    if (position_trajectory)
    {
//      moveDeltaPosition();
      Serial.print("num pts ");
      Serial.print(num_trajectory_points);
      Serial.println(" execute waypoints ");
      executeWaypoints();
    }
  }

  // Update state
  updateState();

  // Print joint states
  publishJointStates();

  // Pause prior to looping again
  delay(1);
}

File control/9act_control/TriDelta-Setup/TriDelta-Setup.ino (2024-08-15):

#include "delta_trajectory.pb.h"
#include "pb_common.h"
#include "pb.h"
#include "pb_encode.h"
#include "pb_decode.h"
#include <Wire.h>
#include <Adafruit_MotorShield.h>
#include <Adafruit_ADS1X15.h>
#include <math.h>
#include "myServoController.h"

#define NUM_MOTORS 9 
#define MY_ID 0

//######################################## Timer ###################
#define CPU_HZ 48000000
#define TIMER_PRESCALER_DIV 1024

//void startTimer(int frequencyHz);
//void setTimerFrequency(int frequencyHz);
//void TC3_Handler();


//################################## Feather MC and ADC Libraries INIT #####################3
Adafruit_MotorShield MC0 = Adafruit_MotorShield(0x61);
Adafruit_MotorShield MC1 = Adafruit_MotorShield(0x60);
Adafruit_MotorShield MC2 = Adafruit_MotorShield(0x62);
//
Adafruit_DCMotor *MC0_M1 = MC0.getMotor(1);
Adafruit_DCMotor *MC0_M2 = MC0.getMotor(2);
Adafruit_DCMotor *MC0_M3 = MC0.getMotor(3);
Adafruit_DCMotor *MC1_M1 = MC1.getMotor(1);
Adafruit_DCMotor *MC1_M2 = MC1.getMotor(2);
Adafruit_DCMotor *MC1_M3 = MC1.getMotor(3);
Adafruit_DCMotor *MC2_M1 = MC2.getMotor(1);
Adafruit_DCMotor *MC2_M2 = MC2.getMotor(2);
Adafruit_DCMotor *MC2_M3 = MC2.getMotor(3);
//
Adafruit_DCMotor* motors[NUM_MOTORS] = {MC0_M1,MC0_M2,MC0_M3,// 1st robot
                                        MC1_M1,MC1_M2,MC1_M3,// 2nd robot
                                        MC2_M1,MC2_M2,MC2_M3,// 3rd robot
                                        };
//Adafruit_DCMotor* motors[NUM_MOTORS] = {MC1_M4};


Adafruit_ADS1015 ADC2;
Adafruit_ADS1015 ADC1;
Adafruit_ADS1015 ADC0;

Adafruit_ADS1015* adcs[NUM_MOTORS] = {&ADC2, &ADC2, &ADC2,//1st robot
                                      &ADC1, &ADC1, &ADC1,//2nd robot
                                      &ADC0, &ADC0, &ADC0,//3rd robot
                                      };

int channels[NUM_MOTORS] = {0,1,2,//1st robot
                            0,1,2,//2nd robot
                            0,1,2,//3rd robot
                            };

//#################################### GLOBAL VARIABLES ##################################//
const int numChars = 3000;
float pi = 3.1415926535;

uint8_t input_cmd[numChars];
bool newData = false;

DeltaMessage message = DeltaMessage_init_zero;
static bool recvInProgress = false;
int ndx = 0;
int ndxx = 0;
char startMarker = 0xA6;
char confMarker = '~';
char endMarker = 0xA7;
int marker_count = 0;
bool skip_trajectory = false;

float trajectory[20][12]; // trajectory[num iters][num motors]
int traj_iter = 0;
bool go = false;
bool reset_flag = false;
bool is_movement_done = false;


myServoController controller(motors, adcs, channels);


void setup() {
  Serial.begin(115200);
  Serial1.begin(115200);
  while (!Serial1) {
    delay(10);
  }
  // set all the base dc motor control pins to outputs
  MC0.begin();
  MC1.begin();
  MC2.begin();
  // start all the ADCs
  ADC2.begin(0x4A);
  ADC1.begin(0x49);
  ADC0.begin(0x48);

  ADC2.setGain(GAIN_ONE);
  ADC1.setGain(GAIN_ONE);
  ADC0.setGain(GAIN_ONE);
  
  controller.init_controller();
  init_comms();

  //startTimer(20); //20 Hz -> 50ms update freq
  
  Serial.print("q"); Serial.print('\t');
  Serial.print("qCmd"); Serial.print('\t');
  Serial.print("q_dot"); Serial.print('\t');
  Serial.println("q_dotCmd");
  
}

float xmin = 0.001;
float xmax = 0.019;

long m_prev = millis();
void loop() {
  
  recvWithStartEndMarkers();
  if (newData) {
    if (decodeNanopbData() & !skip_trajectory) {
        updateTrajectory();
    }
    newData = false;
    ndx = 0;
  }
  executeWaypoints();
  if (traj_iter >= 20 && !reset_flag) {
//    reset();
//    reset_flag = true;
  }
}

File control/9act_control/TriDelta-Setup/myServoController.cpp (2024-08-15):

#include "myServoController.h"
#include <Wire.h>
#include <Adafruit_MotorShield.h>
#include <Adafruit_ADS1X15.h>
#include <math.h>

// 100mm per 1650 bits (3.3V/4.096V)*2^11 (range is +- 4.096V with 1 gain)
// for 100 mm motor: (4.096 / 1650) * 0.1 / 4.096 = 0.000606;
// for 20 mm motor: (4.096 / 1650) * 0.02 / 4.096 = 0.0000121212;
#define ADC2M 0.0000121212 //ADC reading to pos in [m]
// 0-255: * 15 mm/s /25 mm/a
#define CMD2VEL 0.0000920 * 15.0 / 25.0 // Motor command val to vel in [m/s]
// 1/ CMD2VEL (in theory it should be 255/ 0.025 (m/s) = 10200) 
#define VEL2CMD 10869.5652 * 25.0 / 15.0 // vel [m/s] to motor command val [x/+-255]

myServoController::myServoController(Adafruit_DCMotor* motors[NUM_MOTORS], 
                                     Adafruit_ADS1015* adcs[NUM_MOTORS], 
                                     int channels[NUM_MOTORS]) {
  for (int i=0; i<NUM_MOTORS; i++){
    _motors[i] = motors[i];
    _adcs[i] = adcs[i];
    _channels[i] = channels[i];
  }
}


void myServoController::init_controller() {
  // Initialize actuator and encoder
  _millis = millis();
  for (int i=0; i<NUM_MOTORS; i++) {
    _motors[i]->setSpeed(0);
    _motors[i]->run(RELEASE);
    _joint_velocities[i] = 0;
  }
  reset_joints();
  read_joint_positions(); 
}

void myServoController::reset_joints() {
  read_joint_positions();
  float xf[NUM_MOTORS] = {0.001, 0.001, 0.001,
                          0.001, 0.001, 0.001,
                          0.001, 0.001, 0.001};
  ramp2pos(xf, 15.0/1000.0, 7.5/1000.0);
  for (int i=0; i<NUM_MOTORS; i++) {
    _motors[i]->run(RELEASE);
  }
}

void myServoController::stop_moving() {
  read_joint_positions();
  for (int i=0; i<NUM_MOTORS; i++) {
    _motors[i]->run(RELEASE);
  }
}

void myServoController::read_joint_positions() {
  for (int i=0; i<NUM_MOTORS; i++) {
    int ADC_val = _adcs[i]->readADC_SingleEnded(_channels[i]);
    _joint_positions[i] = ADC2M*ADC_val;
  }
}

void myServoController::update_state() {
  for (int i=0; i<NUM_MOTORS; i++) {
    _prev_joint_positions[i] = _joint_positions[i];
  }
  long curr_millis = millis();
  _delta_millis = curr_millis - _millis;
  _millis = curr_millis;
  read_joint_positions();
  for (int i=0; i<NUM_MOTORS; i++) {
    _joint_velocities[i] = (_joint_positions[i] - _prev_joint_positions[i])/(_delta_millis * 0.001);
  }
  
}

void myServoController::print_state() {
  Serial.println("Joint Positions");
  for (int i=0; i<NUM_MOTORS; i++) {
    Serial.print(1000*_joint_positions[i]); Serial.print('\t');
  }
  Serial.println();
  Serial.println("Joint Velocities");
  for (int i=0; i<NUM_MOTORS; i++) {
    Serial.print(1000*_joint_velocities[i]); Serial.print('\t');
  }
  Serial.println();
}

void myServoController::cmdPos(float qCmd[]) {
  for(int i=0; i<NUM_MOTORS; i++) {
    _joint_positionsCmd[i] = qCmd[i];
  }
}

void myServoController::cmdVel(float q_dotCmd[]) {
  for (int i=0; i<NUM_MOTORS; i++){
    _joint_velocitiesCmd[i] = q_dotCmd[i];
    _refCmd[i] = q_dotCmd[i] * VEL2CMD;
  }
}

void myServoController::positional_PID(float PID_Cmd[NUM_MOTORS]) {
  for (int i=0; i<NUM_MOTORS; i++) {
    float error = _joint_positionsCmd[i] - _joint_positions[i];
    _cmdPos_integral_error[i] = _cmdPos_integral_error[i] + error * (0.001*_delta_millis);
    _cmdPos_derivative_error[i] = (error - _cmdPos_error[i]) / (0.001*_delta_millis);
    _cmdPos_error[i] = error;
  
    PID_Cmd[i] = (_cmdPos_Kp*_cmdPos_error[i] + 
                  _cmdPos_Ki*_cmdPos_integral_error[i] + 
                  _cmdPos_Kd*_cmdPos_derivative_error[i]);
  }
}

void myServoController::send_motorCmd() {
  for (int i=0; i<NUM_MOTORS; i++) {
    int motor_cmd_val = _motorCmd[i];
    motor_cmd_val = min(max(motor_cmd_val, -255), 255); // Clip to safe bounds
    if (motor_cmd_val > 20) {
      _motors[i]->run(FORWARD);
    } else if (motor_cmd_val < 20){
      _motors[i]->run(BACKWARD);
    } else {
      _motors[i]->run(RELEASE);
    }
    _motors[i]->setSpeed((uint8_t)(abs(motor_cmd_val)));
  }
}

void myServoController::driveController() {
  update_state();
  
  float PID_Cmd[NUM_MOTORS];
  positional_PID(PID_Cmd);

  for (int i=0; i<NUM_MOTORS; i++) {
    _motorCmd[i] = (int)(_refCmd[i] + _lambda_cmdPos*PID_Cmd[i]);
  }

  send_motorCmd();
}

//********************* Trajectories ******************************//
void myServoController::ramp_pos(float t, float qCmd[NUM_MOTORS], float x0[NUM_MOTORS], float xf[NUM_MOTORS], float v[NUM_MOTORS], float amax_ref) {
  // Modify qCmd with the x(t) values of a ramp traj
  float vmax;
  float amax;
  
  for (int i=0; i<NUM_MOTORS; i++) {
    float delta_x = xf[i] - x0[i];
    if (delta_x < 0) {
      vmax = -v[i];
      amax = -amax_ref;
    } else {
      vmax = v[i];
      amax = amax_ref;
    }
    float tr = min(delta_x/vmax, vmax/amax);
    float tm = max(0, delta_x/vmax - vmax/amax);
    // Piece wise integration
    if (t < tr) {
      qCmd[i] = x0[i] + 0.5*amax*pow(t,2);
    } else if (tr <= t & t < tr + tm) {
      qCmd[i] = x0[i] + (0.5*amax*pow(tr,2)) + vmax*(t-tr);
    } else if (tr + tm <= t & t < 2*tr + tm) {
      qCmd[i] = x0[i] + (0.5*amax*pow(tr,2)) + (vmax*tm) + (vmax*(t-tm-tr) - 0.5*amax*pow(t-tm-tr,2));
    } else {
      qCmd[i] = xf[i];
    }
  }
}

void myServoController::ramp_vel(float t, float q_dotCmd[NUM_MOTORS], float x0[NUM_MOTORS], float xf[NUM_MOTORS], float v[NUM_MOTORS], float amax_ref) {
  // Modify q_dotCmd with the v(t) values of a ramp traj
  float vmax;
  float amax;
  
  for (int i=0; i<NUM_MOTORS; i++) {
    float delta_x = xf[i] - x0[i];
    float pure_PID_tol = 0.003; // If dx is small, ref commands may cause overshoot
    if (delta_x < 0) {
      vmax = -v[i];
      amax = -amax_ref;
    } else {
      vmax = v[i];
      amax = amax_ref;
    }
    float tr = min(delta_x/vmax, vmax/amax);
    float tm = max(0, delta_x/vmax - vmax/amax);
    // Piece wise integration
    if (t < tr) {
      q_dotCmd[i] = amax*t;
    } else if (tr <= t & t < tr + tm) {
      q_dotCmd[i] = vmax;
    } else if (tr + tm <= t & t < 2*tr + tm) {
      q_dotCmd[i] = vmax - amax*(t-tr-tm);
    } else {
      q_dotCmd[i] = 0.0;
    }
    if (abs(delta_x) < pure_PID_tol) {
      q_dotCmd[i] = 0.0;
    }
  }
}

float myServoController::ramp_tf(float tf[NUM_MOTORS], float x0[NUM_MOTORS], float xf[NUM_MOTORS], float vmax, float amax) {
  float tf_max = 0;
  float tr;
  float tm;
  float delta_x;
  for (int i=0; i<NUM_MOTORS; i++) {
    delta_x = abs(xf[i] - x0[i]);
    tr = min(delta_x/vmax, vmax/amax);
    tm = max(0, delta_x/vmax - vmax/amax);
    tf[i] = 2*tr + tm;
    tf_max = max(tf_max, tf[i]);
  }
  return tf_max;
}
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
